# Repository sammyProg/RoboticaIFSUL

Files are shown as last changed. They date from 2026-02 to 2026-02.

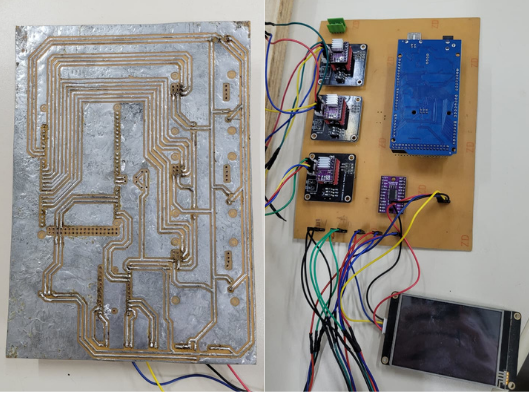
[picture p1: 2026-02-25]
PCB EasyEDA/PCB final.png

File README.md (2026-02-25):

Projeto e Desenvolvimento de um Manipulador Robótico Antropomórfico de 6 GDL (Parcialmente Atuado) para o Ensino da Cinemática Direta

Descrição

Este repositório reúne os arquivos de apoio ao projeto de um manipulador robótico antropomórfico de seis graus de liberdade (6 GDL), parcialmente atuado e impresso em 3D, desenvolvido com finalidade didática para o ensino de cinemática direta.
O projeto foi concebido com foco em:
- visualização prática de conceitos de cinemática direta;
- integração entre modelagem mecânica, eletrônica embarcada e interface homem-máquina;
- validação experimental por comparação entre resultados obtidos via firmware embarcado, MATLAB e visão computacional com marcadores ArUco. 
Observação: embora o manipulador possua 6 GDL, o protótipo é parcialmente atuado, com 3 juntas motorizadas e instrumentadas para os experimentos didáticos, enquanto as demais juntas permanecem fixas no escopo proposto. 

Conteúdo deste repositório

Este repositório foi organizado para concentrar os materiais técnicos utilizados no projeto, incluindo:
- Código-fonte do sistema embarcado (Firmware)
- Controle de motores, leitura de sensores, comunicação com interface e cálculo de cinemática direta embarcada.
- Código-fonte de validação com ArUco
- Rotinas de visão computacional para medição/estimativa de pose e comparação com os resultados do sistema.

Desenhos de referência em SolidWorks
- Desenhos de peças (elos, base, engrenagens etc.)
- Desenho de montagem de conjuntos
- Referências dimensionais para fabricação e montagem do protótipo

Documentação complementar (opcional)
- Esquemático EasyEDA
- Interface IHM Nextion
- Desenho de apoio 2D
  
Materiais auxiliares, imagens, PDFs e instruções para reprodução parcial do sistema.

Conteúdo deste repositório

Este repositório foi organizado para concentrar os materiais técnicos utilizados no projeto, incluindo:
- Código-fonte do sistema embarcado (Firmware)
- Controle de motores, leitura de sensores, comunicação com interface e cálculo de cinemática direta embarcada.
- Código-fonte de validação com ArUco
- Rotinas de visão computacional para medição/estimativa de pose e comparação com os resultados do sistema.
- Desenhos de referência em SolidWorks
- Desenhos de peças (elos, base, engrenagens etc.)
- Desenho de montagem de conjuntos
- Referências dimensionais para fabricação e montagem do protótipo
- Documentação complementar (opcional)
- Materiais auxiliares, imagens, PDFs e instruções para reprodução parcial do sistema.

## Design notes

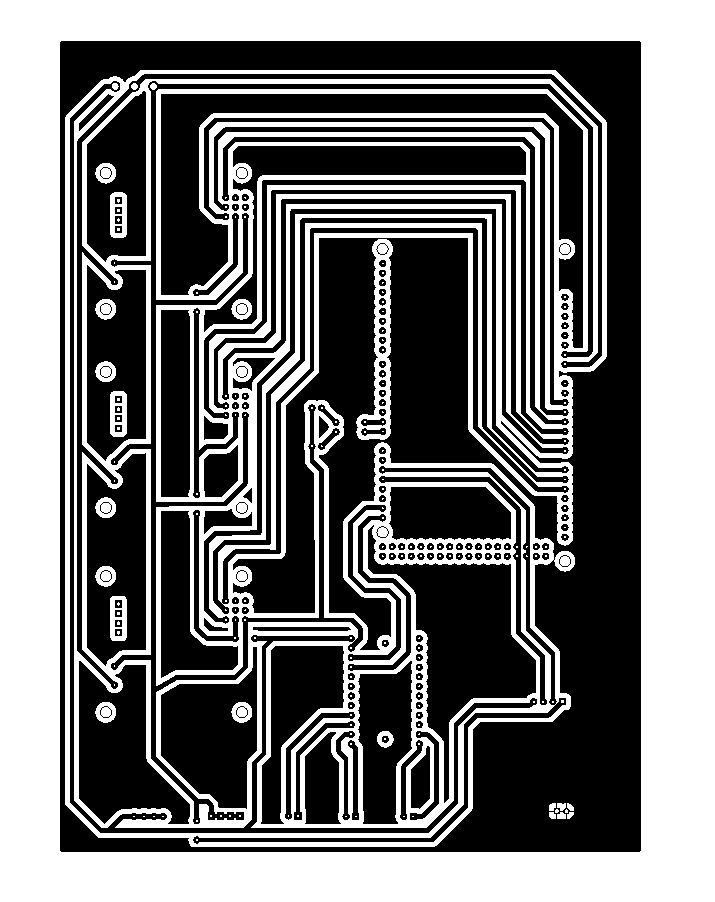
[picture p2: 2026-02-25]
PCB EasyEDA/PCB_PCB_PCB-Braço_2_2026-02-13.png

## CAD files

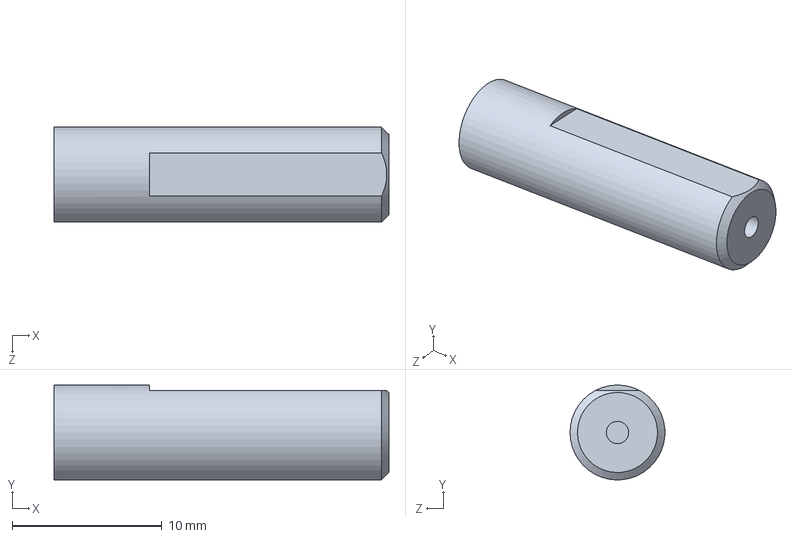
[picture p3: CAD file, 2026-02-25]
SolidWorks/Peças/Conjunto Motor/Eixo motor Nema23.SLDPRT
22.4 x 6.35 x 6.35 mm

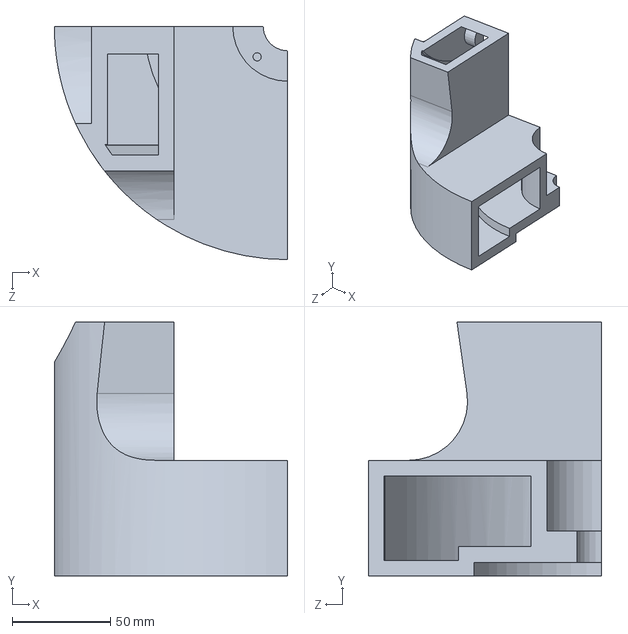
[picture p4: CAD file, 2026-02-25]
SolidWorks/Peças/Elo 1/Elo 1 quadrante 3 baixo.SLDPRT
119.0 x 129.5 x 119.0 mm

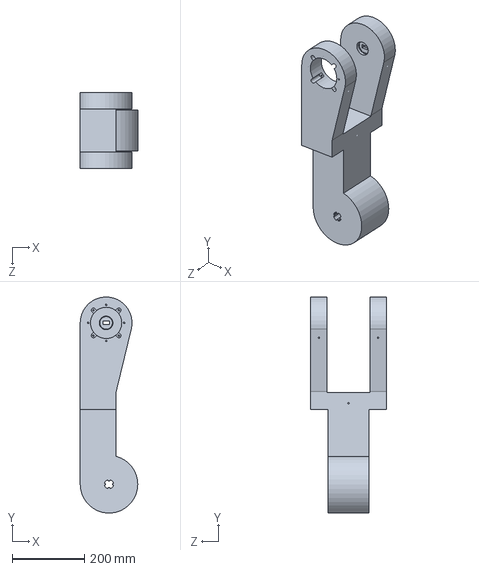
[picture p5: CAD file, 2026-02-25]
SolidWorks/Peças/Elo 2/Elo 2 braço ROB.SLDPRT
160.0 x 599.6 x 210.0 mm

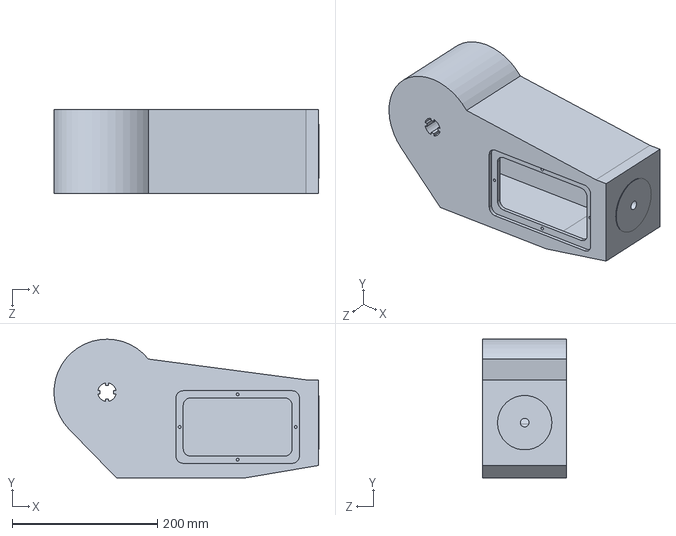
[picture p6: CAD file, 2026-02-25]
SolidWorks/Peças/Elo 3/Elo 3 braço rob.SLDPRT
365.0 x 191.0 x 115.5 mm

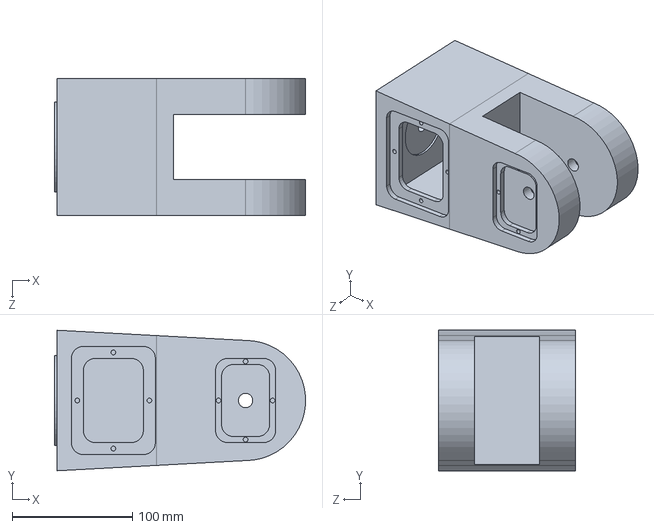
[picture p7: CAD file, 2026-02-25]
SolidWorks/Peças/Elo 4/Elo 4 braço ROB.SLDPRT
208.9 x 117.0 x 114.0 mm

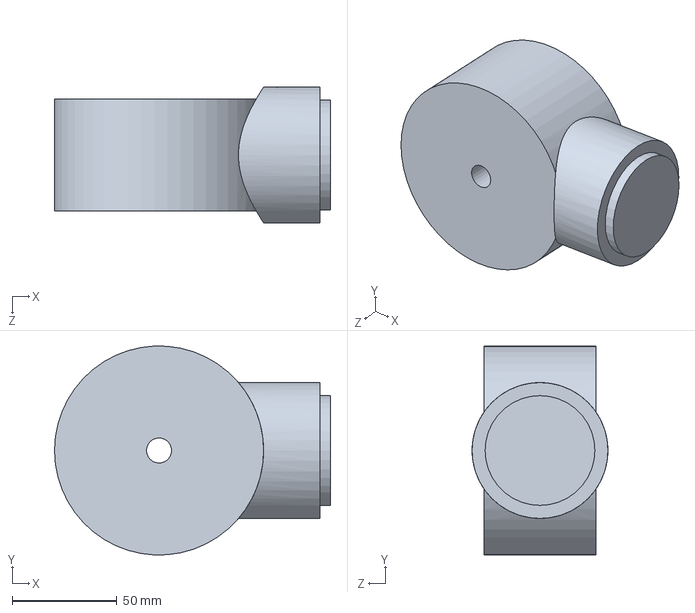
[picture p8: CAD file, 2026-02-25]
SolidWorks/Peças/Elo 5/Elo 5 braço ROB.SLDPRT
132.0 x 99.9 x 65.0 mm

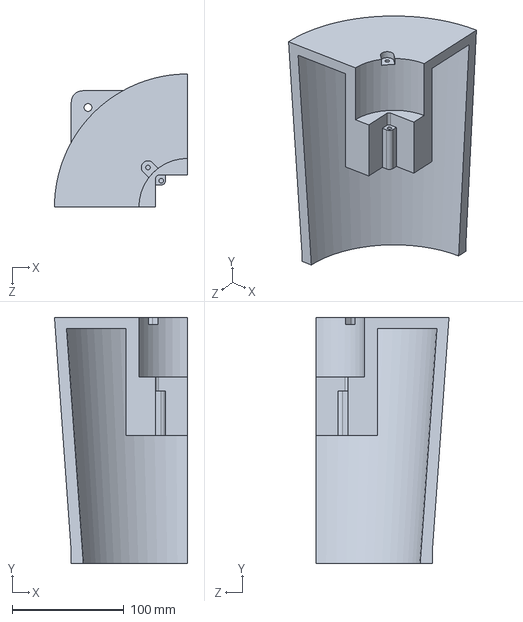
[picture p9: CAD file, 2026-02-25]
SolidWorks/Peças/Elo Base/Base braço ROB quadrante 4.SLDPRT
119.0 x 220.0 x 119.0 mm

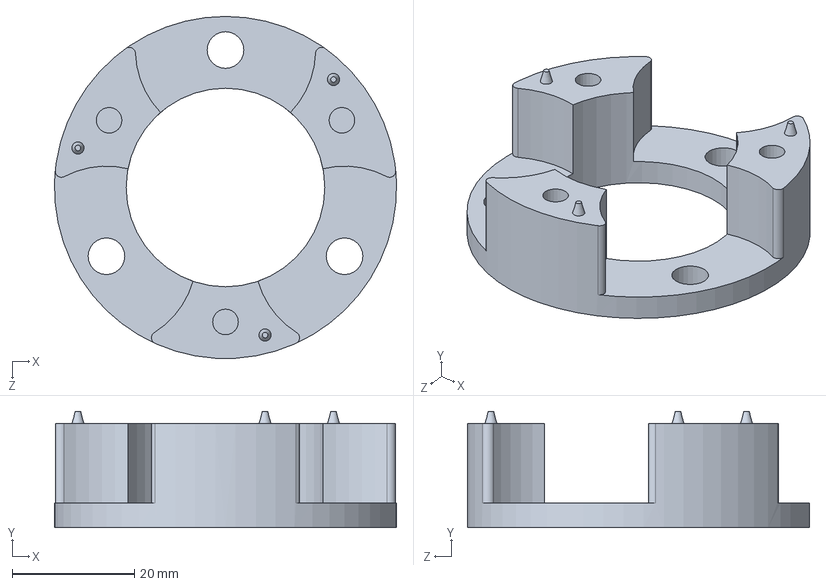
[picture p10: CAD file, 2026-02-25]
SolidWorks/Peças/Engrenagens dentes retos/Peça 5.SLDPRT
56.0 x 19.0 x 56.0 mm

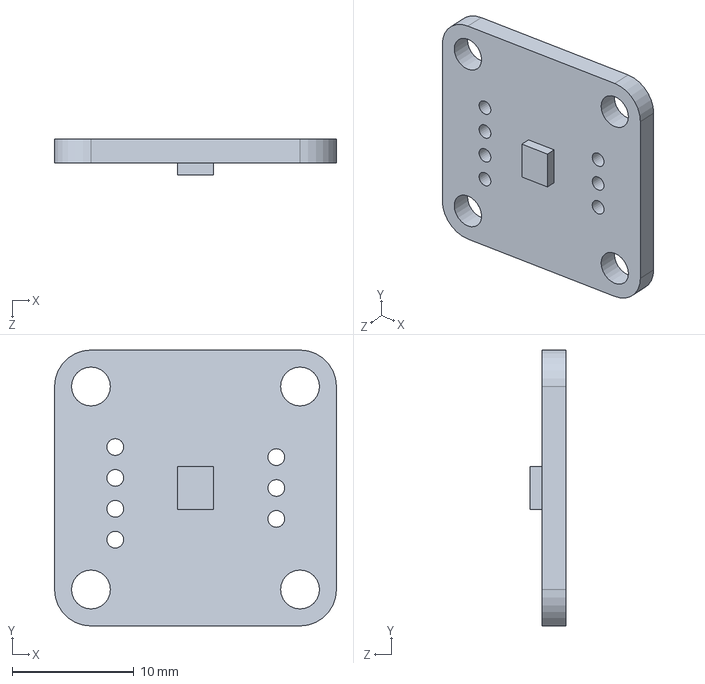
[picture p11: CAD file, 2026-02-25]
SolidWorks/Peças/Conjunto Motor/AS5600.SLDPRT
23.2 x 22.7 x 3.00 mm

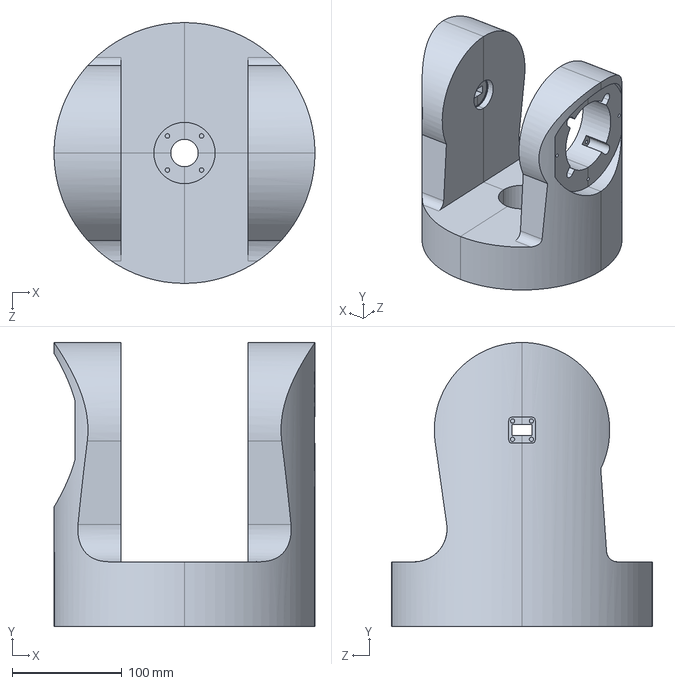
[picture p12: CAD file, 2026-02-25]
SolidWorks/Peças/Elo 1/Elo 1 braço ROB.SLDPRT
238.0 x 259.1 x 238.0 mm

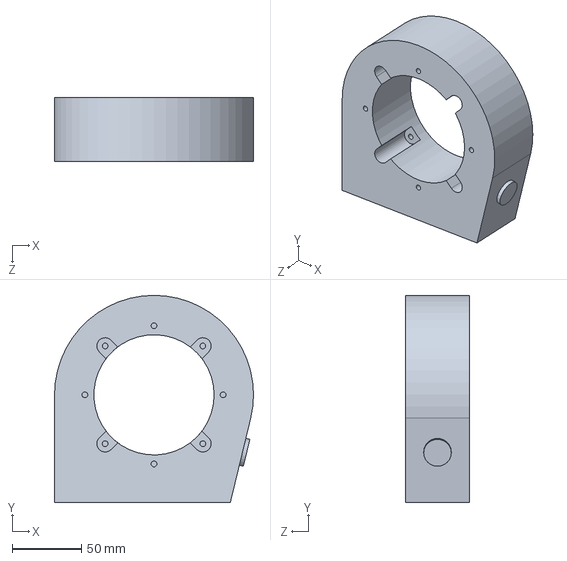
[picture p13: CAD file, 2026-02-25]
SolidWorks/Peças/Elo 2/Elo 2 braço ROB pt 5.SLDPRT
144.0 x 150.0 x 46.0 mm

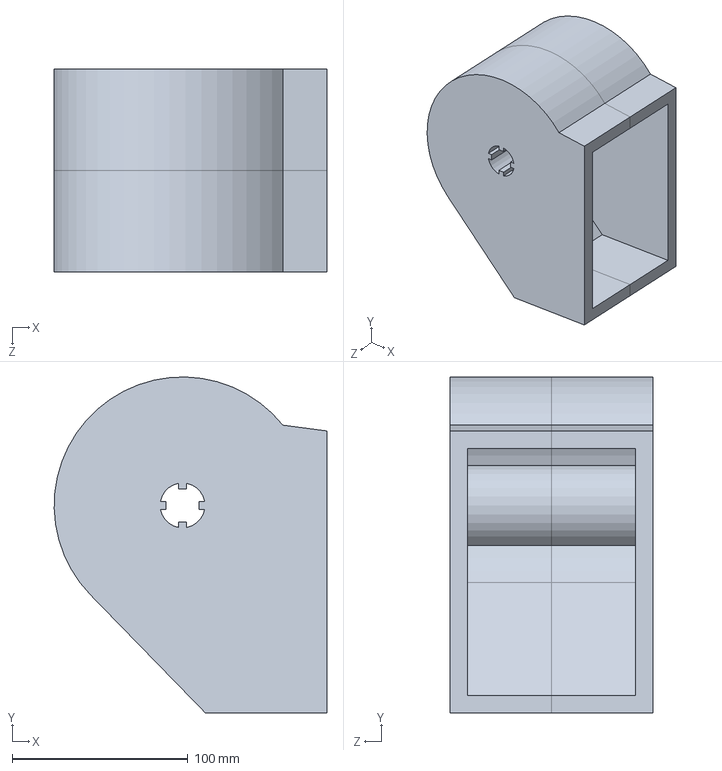
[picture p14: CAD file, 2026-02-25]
SolidWorks/Peças/Elo 3/Elo 3 braço rob pt3.SLDPRT
155.0 x 191.0 x 115.5 mm

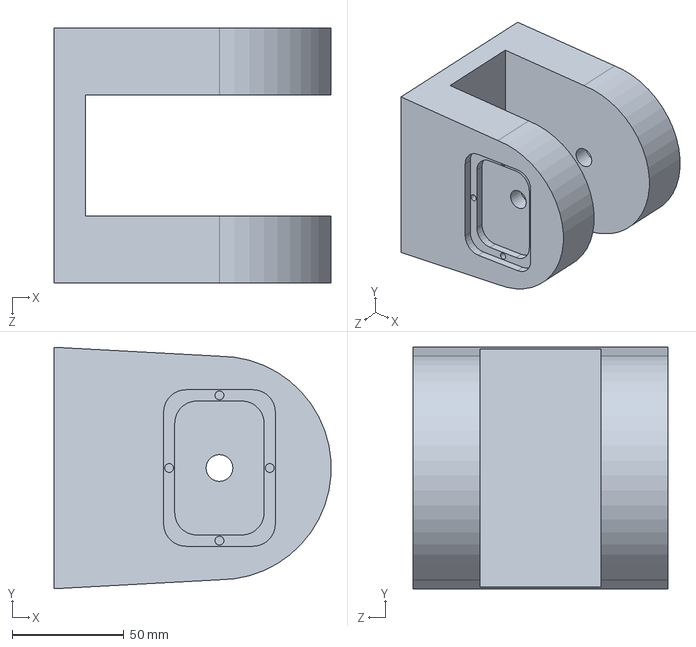
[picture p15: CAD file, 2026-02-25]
SolidWorks/Peças/Elo 4/Elo 4 braço ROB pt2.SLDPRT
123.9 x 108.0 x 114.0 mm

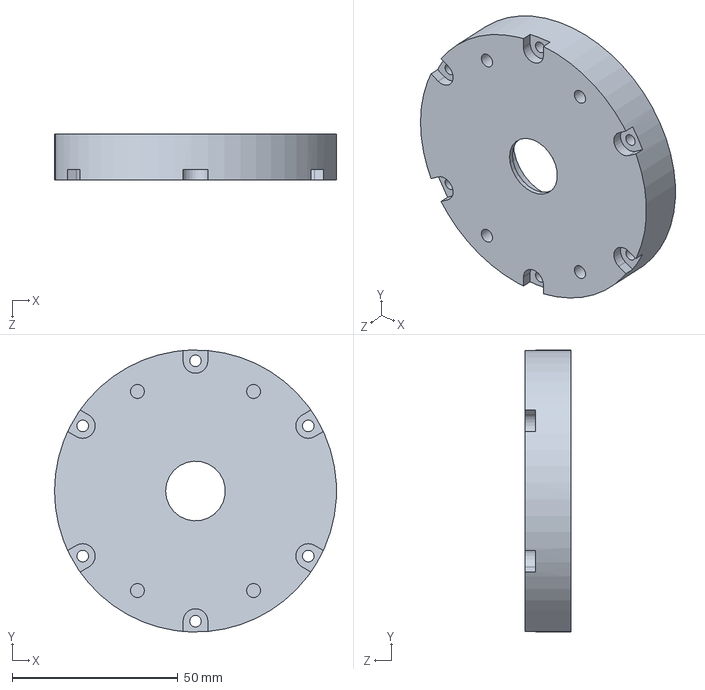
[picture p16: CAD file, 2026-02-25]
SolidWorks/Peças/Engrenagens dentes retos/Peça 8.SLDPRT
85.0 x 85.0 x 14.0 mm

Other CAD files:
SolidWorks/Montagens/Conjunto Motor/MontConjuntoMotor.SLDASM
SolidWorks/Montagens/Engrenagens Planetárias/Montagem Redução dentes retos elo 1.SLDASM
SolidWorks/Montagens/Engrenagens Planetárias/Montagem Redução dentes retos.SLDASM
SolidWorks/Peças/Elo Base/Base braço ROB quadrante 2.SLDPRT
SolidWorks/Peças/Conjunto Motor/Pino central 3mm v2.SLDPRT
SolidWorks/Peças/Conjunto Motor/Pino central.SLDPRT
SolidWorks/Peças/Conjunto Motor/Suporte.SLDPRT
SolidWorks/Peças/Elo 1/Elo 1 quadrante 1 baixo.SLDPRT
SolidWorks/Peças/Elo 1/Elo 1 quadrante 1 cima.SLDPRT
SolidWorks/Peças/Elo 1/Elo 1 quadrante 1.SLDPRT
SolidWorks/Peças/Elo 1/Elo 1 quadrante 2 baixo.SLDPRT
SolidWorks/Peças/Elo 1/Elo 1 quadrante 2 cima.SLDPRT
SolidWorks/Peças/Elo 1/Elo 1 quadrante 2.SLDPRT
SolidWorks/Peças/Elo 1/Elo 1 quadrante 3 cima.SLDPRT
SolidWorks/Peças/Elo 1/Elo 1 quadrante 3.SLDPRT
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

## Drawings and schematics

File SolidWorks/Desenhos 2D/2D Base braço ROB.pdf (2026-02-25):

B

A

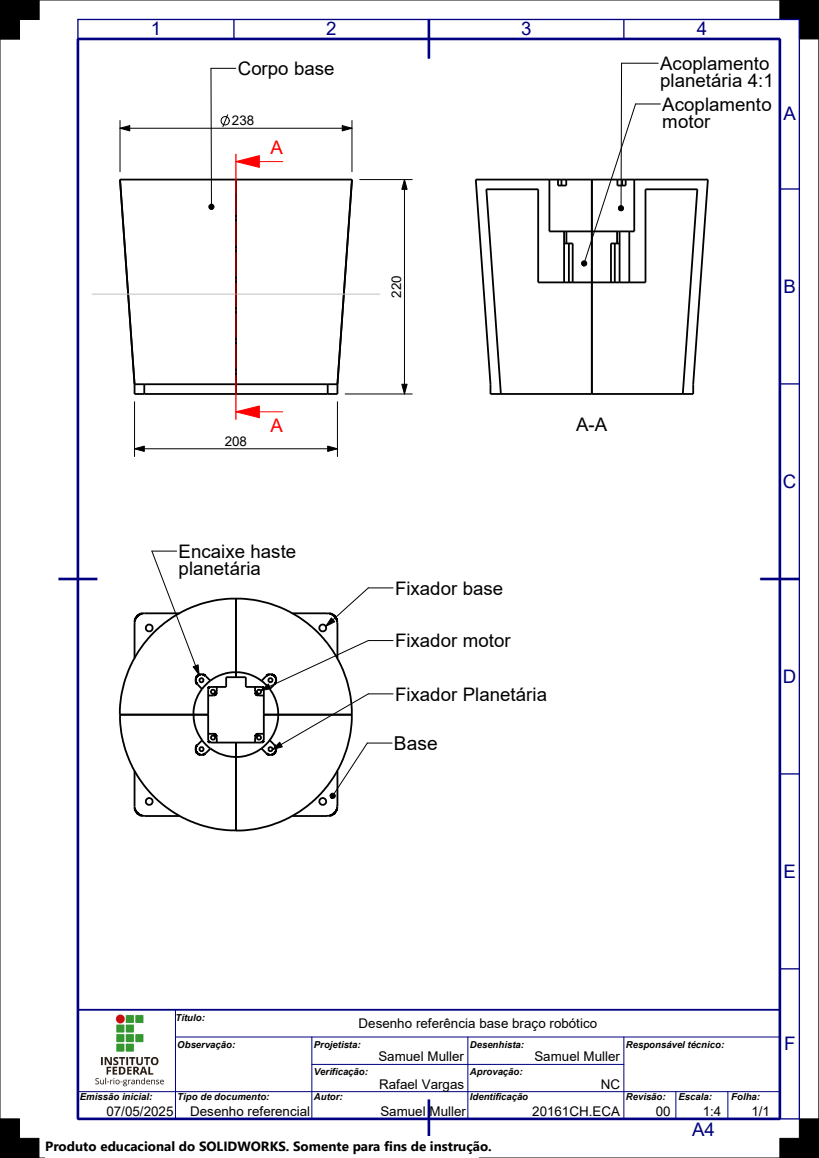
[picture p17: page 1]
Fixador motor; Base; Fixador base; Fixador Planetária; Encaixe haste planetária; Corpo base; Acoplamento planetária 4:1 Acoplamento motor

Título: Desenho referência base braço robótico

Observação: | Projetista: Samuel Muller | Desenhista: Samuel Muller | Responsável técnico:

Verificação: Rafael Vargas | Aprovação: NC

Emissão inicial: 07/05/2025 | Tipo de documento: Desenho referencial | Autor: Samuel Muller | | Identificação | Revisão: 00 20161CH.ECA | Escala: | Folha: 1/1 1:4

Produto educacional do SOLIDWORKS. Somente para fins de instrução.

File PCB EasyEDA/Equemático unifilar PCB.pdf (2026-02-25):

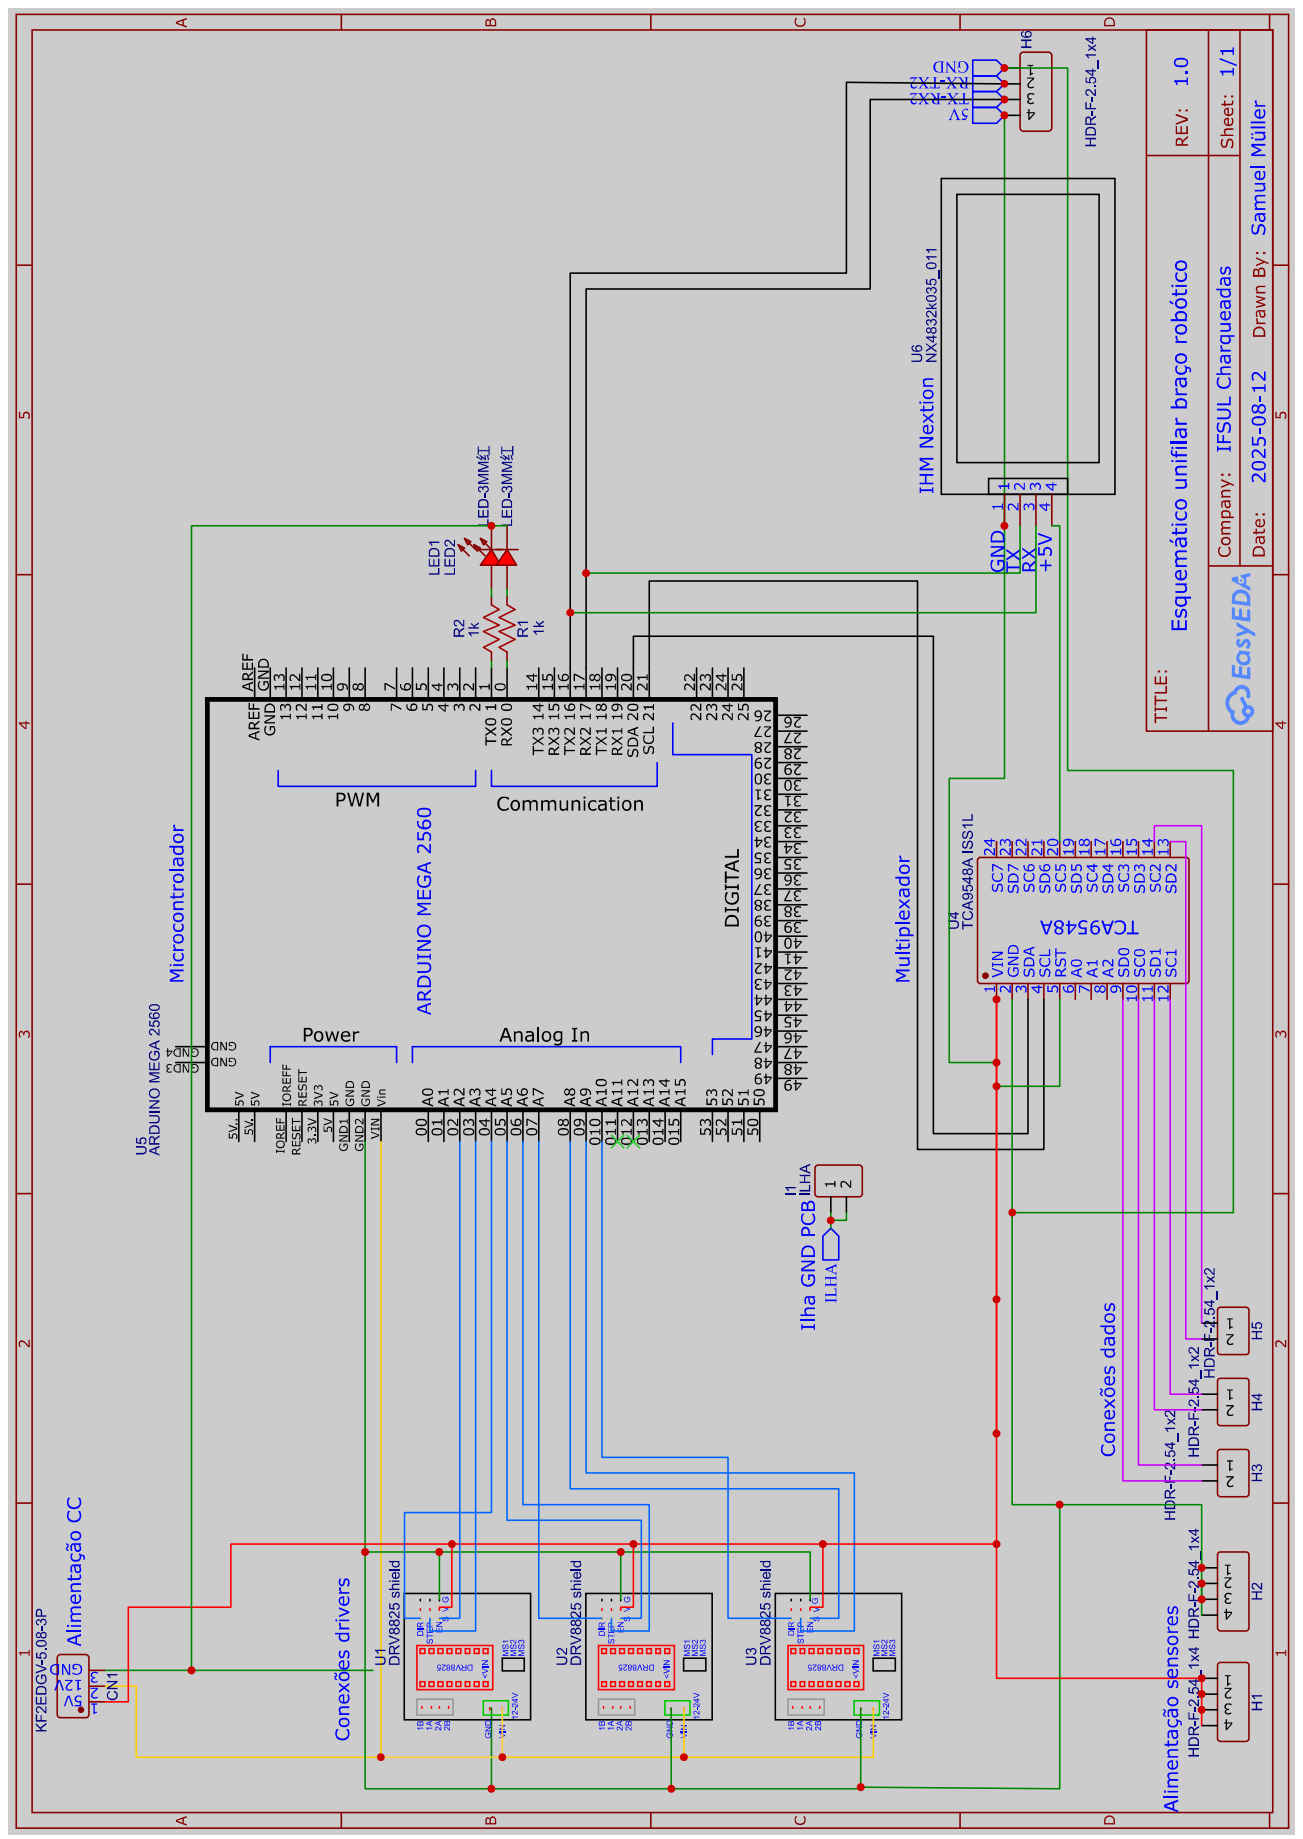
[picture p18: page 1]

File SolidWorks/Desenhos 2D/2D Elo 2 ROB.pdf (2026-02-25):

A

1 | 2 | 3

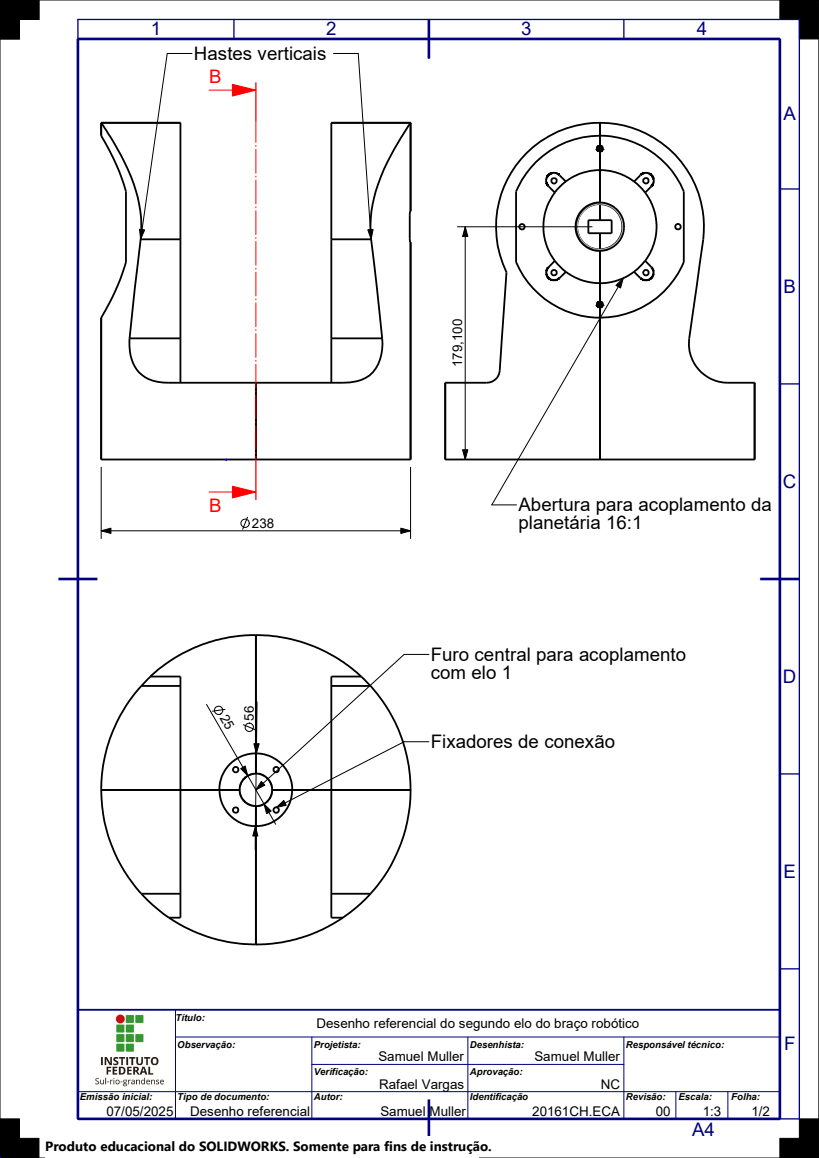
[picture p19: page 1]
Hastes verticais

Desenho referencial do segundo elo do braço robótico ¹⁷⁹,100

Abertura para acoplamento da
planetária 16:1

Furo central para acoplamento
com elo 1

Fixadores de conexão

Título:

Observação: | Projetista: Samuel Muller | Desenhista: Samuel Muller | Responsável técnico:

Verificação: Rafael Vargas | Aprovação: NC

Emissão inicial: 07/05/2025 | Tipo de documento: Desenho referencial | Autor: Samuel Muller | | Identificação | Revisão: 00 20161CH.ECA | Escala: | Folha: 1/2 1:3

Produto educacional do SOLIDWORKS. Somente para fins de instrução.

# Compartimento rolamento

# Abertura para leitura do sensor

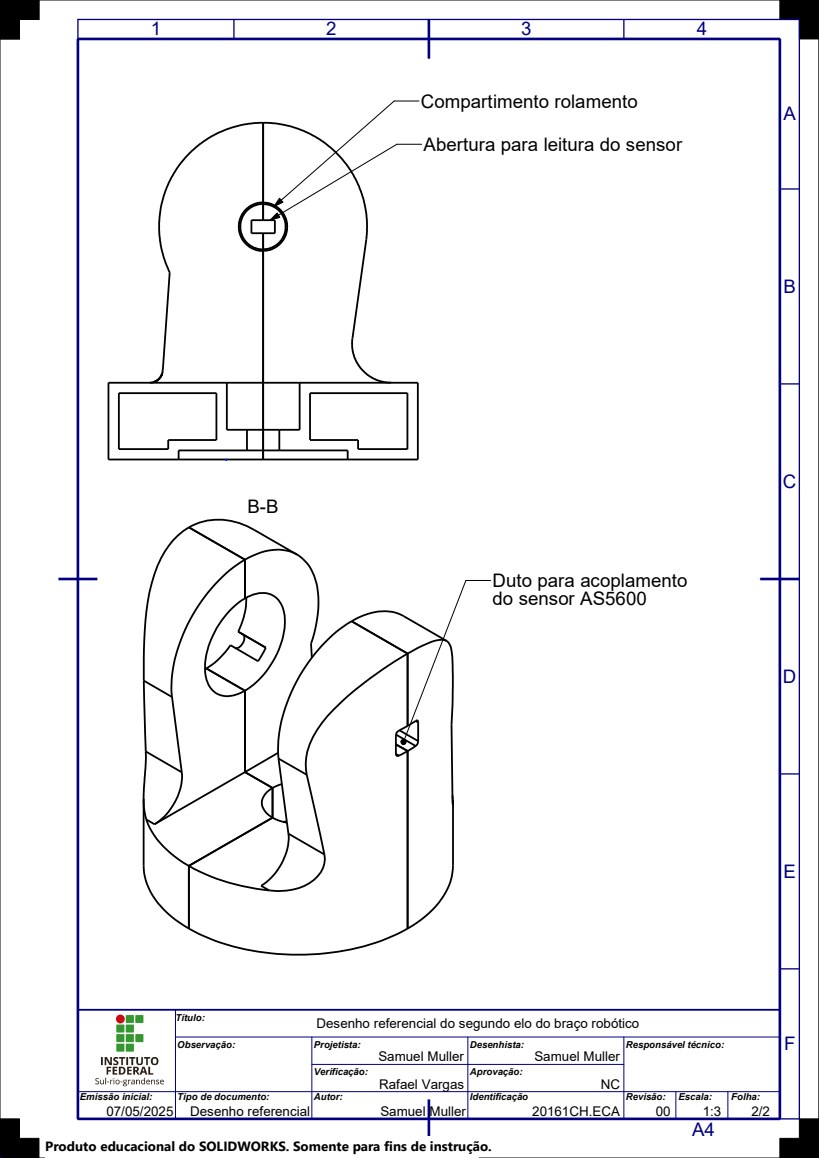
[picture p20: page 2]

Duto para acoplamento
do sensor AS5600

Título: Desenho referencial do segundo elo do braço robótico

Observação: | Projetista: Samuel Muller | Desenhista: Samuel Muller | Responsável técnico:

Verificação: Rafael Vargas | Aprovação: NC

Emissão inicial: 07/05/2025 | Tipo de documento: Desenho referencial | Autor: Samuel Muller | | Identificação | Revisão: 00 20161CH.ECA | Escala: | Folha: 2/2 1:3

Produto educacional do SOLIDWORKS. Somente para fins de instrução.

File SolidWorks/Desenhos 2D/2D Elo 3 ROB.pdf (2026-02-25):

3

B

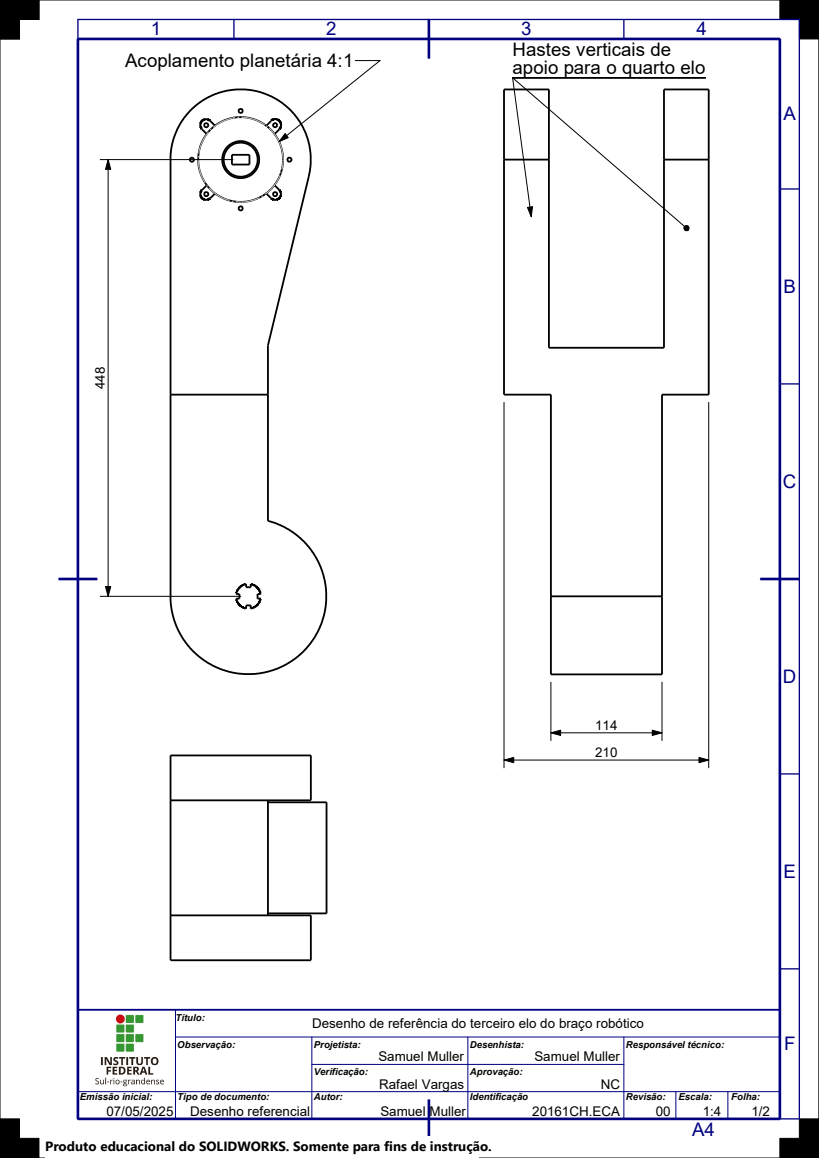
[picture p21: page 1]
Acoplamento planetária 4:1; apoio para o quarto elo

Hastes verticais de

Desenho de referência do terceiro elo do braço robótico ⁴⁴⁸

Título:

Observação: | Projetista: Samuel Muller | Desenhista: Samuel Muller | Responsável técnico:

Verificação: Rafael Vargas | Aprovação: NC

Emissão inicial: 07/05/2025 | Tipo de documento: Desenho referencial | Autor: Samuel Muller | | Identificação | Revisão: 00 20161CH.ECA | Escala: | Folha: 1/2 1:4

Produto educacional do SOLIDWORKS. Somente para fins de instrução.

B

A

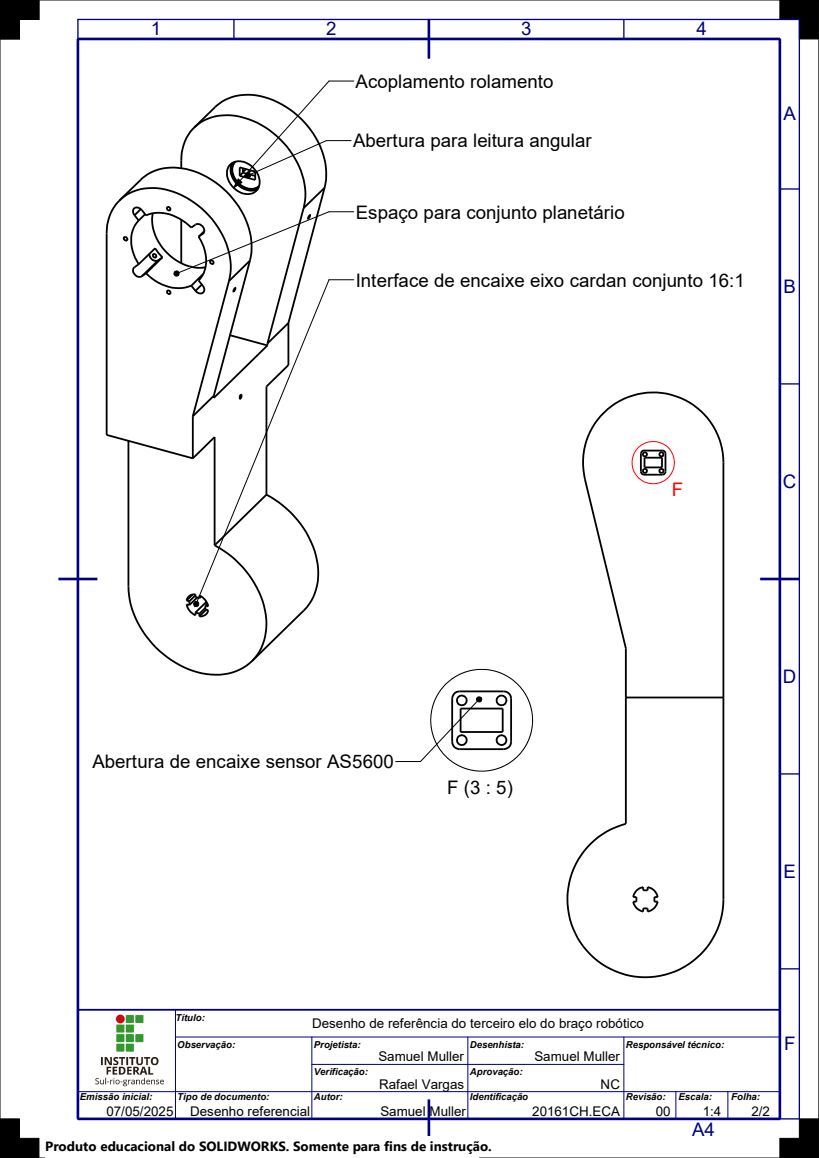
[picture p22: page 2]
Acoplamento rolamento

Abertura para leitura angular

Espaço para conjunto planetário

Interface de encaixe eixo cardan conjunto 16:1

Abertura de encaixe sensor AS5600

Título: Desenho de referência do terceiro elo do braço robótico

Observação: | Projetista: Samuel Muller | Desenhista: Samuel Muller | Responsável técnico:

Verificação: Rafael Vargas | Aprovação: NC

Emissão inicial: 07/05/2025 | Tipo de documento: Desenho referencial | Autor: Samuel Muller | | Identificação | Revisão: 00 20161CH.ECA | Escala: | Folha: 2/2 1:4

Produto educacional do SOLIDWORKS. Somente para fins de instrução.

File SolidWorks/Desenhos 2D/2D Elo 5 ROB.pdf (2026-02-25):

2 3

B

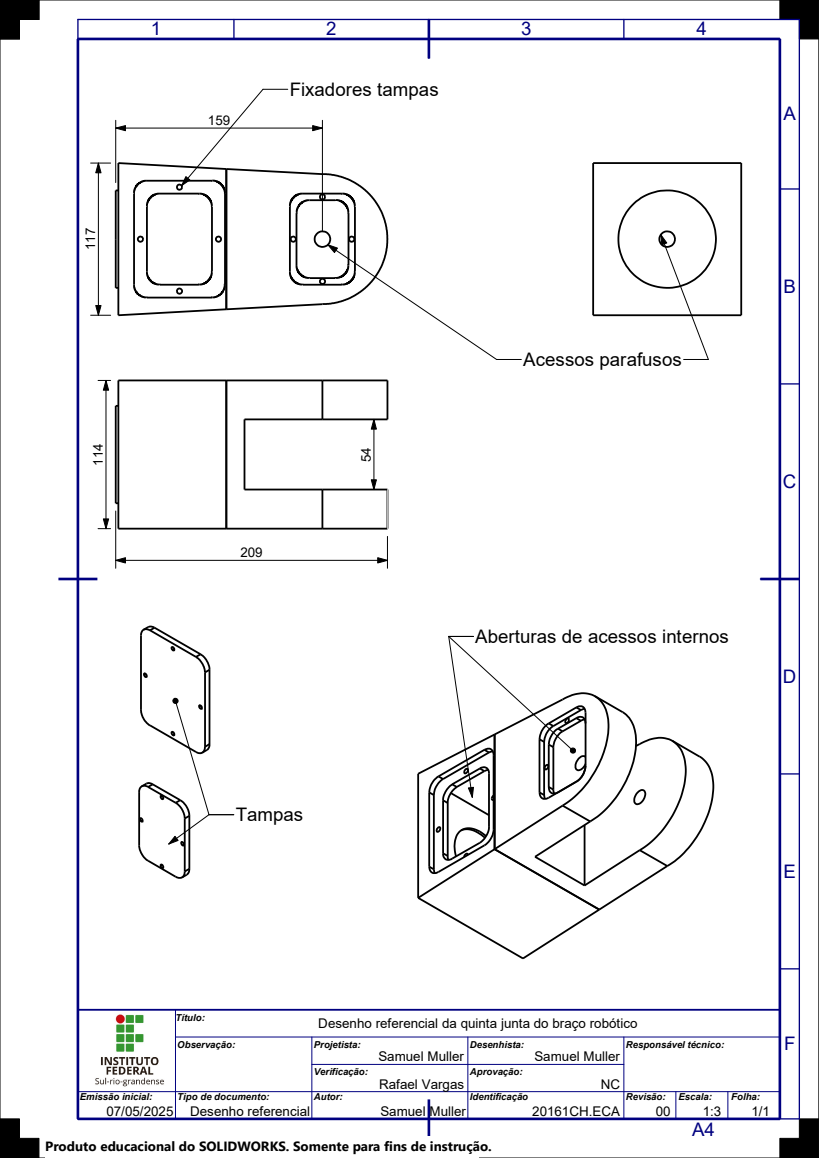
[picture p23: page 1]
Acessos parafusos; Fixadores tampas; Tampas

Aberturas de acessos internos

Título: Desenho referencial da quinta junta do braço robótico

Observação: | Projetista: Samuel Muller | Desenhista: Samuel Muller | Responsável técnico:

Verificação: Rafael Vargas | Aprovação: NC

Emissão inicial: 07/05/2025 | Tipo de documento: Desenho referencial | Autor: Samuel Muller | | Identificação | Revisão: 00 20161CH.ECA | Escala: | Folha: 1/1 1:3

Produto educacional do SOLIDWORKS. Somente para fins de instrução.

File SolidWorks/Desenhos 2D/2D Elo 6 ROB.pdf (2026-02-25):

3

B

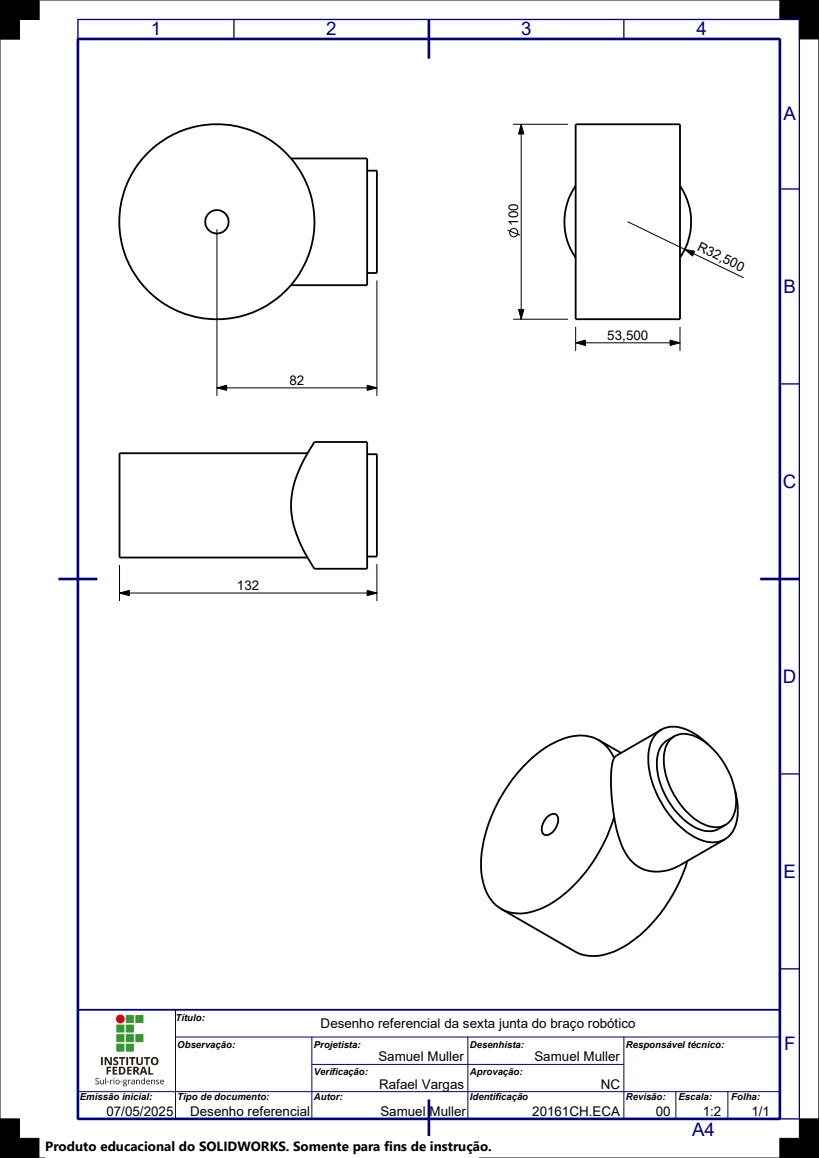
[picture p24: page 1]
53,500 ¹⁰⁰

Título: Desenho referencial da sexta junta do braço robótico

Observação: | Projetista: Samuel Muller | Desenhista: Samuel Muller | Responsável técnico:

Verificação: Rafael Vargas | Aprovação: NC

Emissão inicial: 07/05/2025 | Tipo de documento: Desenho referencial | Autor: Samuel Muller | | Identificação | Revisão: 00 20161CH.ECA | Escala: | Folha: 1/1 1:2

Produto educacional do SOLIDWORKS. Somente para fins de instrução.

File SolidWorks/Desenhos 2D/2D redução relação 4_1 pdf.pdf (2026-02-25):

A A

## Tampa superior

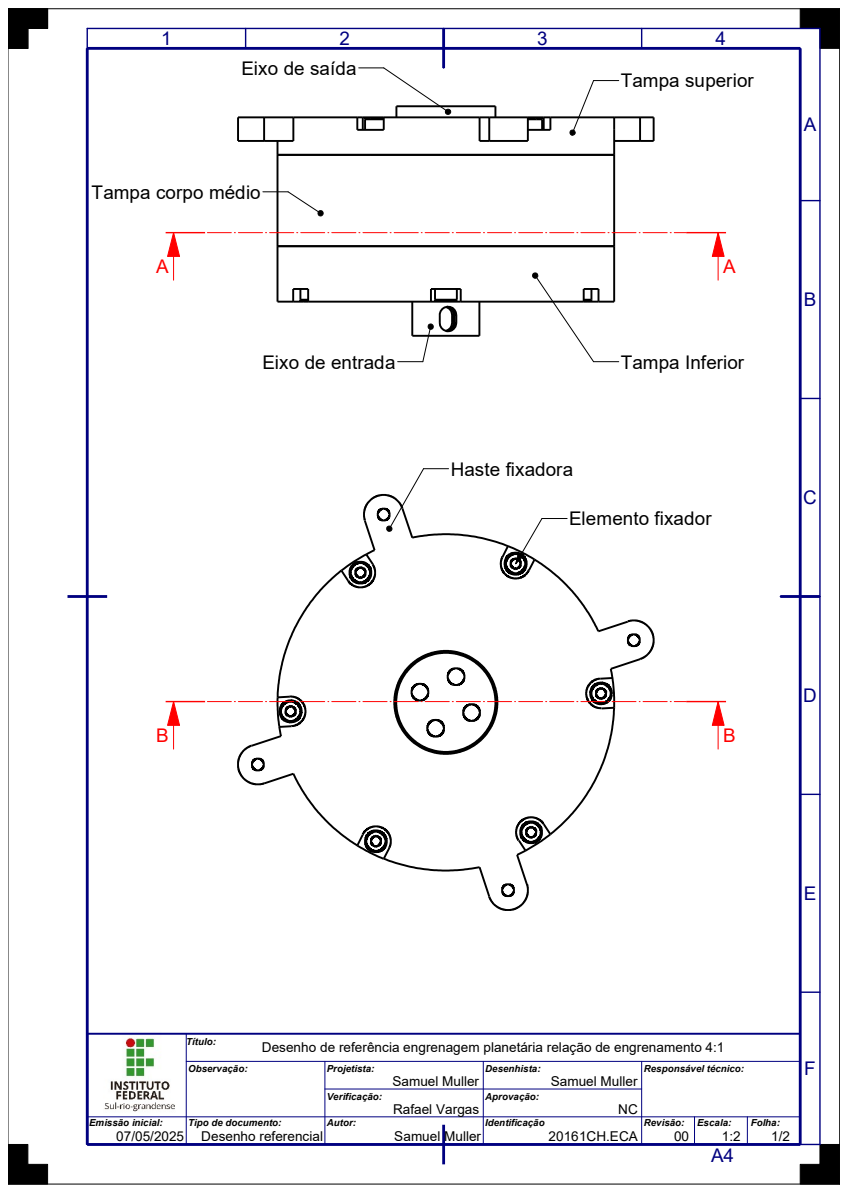
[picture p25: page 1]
Eixo de entrada; Tampa Inferior; Haste fixadora; Elemento fixador

Eixo de saída

Tampa corpo médio

Título: Desenho de referência engrenagem planetária relação de engrenamento 4:1

Observação: | Projetista: Samuel Muller | Desenhista: Samuel Muller | Responsável técnico:

Verificação: Rafael Vargas | Aprovação: NC

Emissão inicial: 07/05/2025 | Tipo de documento: Desenho referencial | Autor: Samuel Muller | | Identificação | Revisão: 00 20161CH.ECA | Escala: | Folha: 1/2 1:2

2 3

A

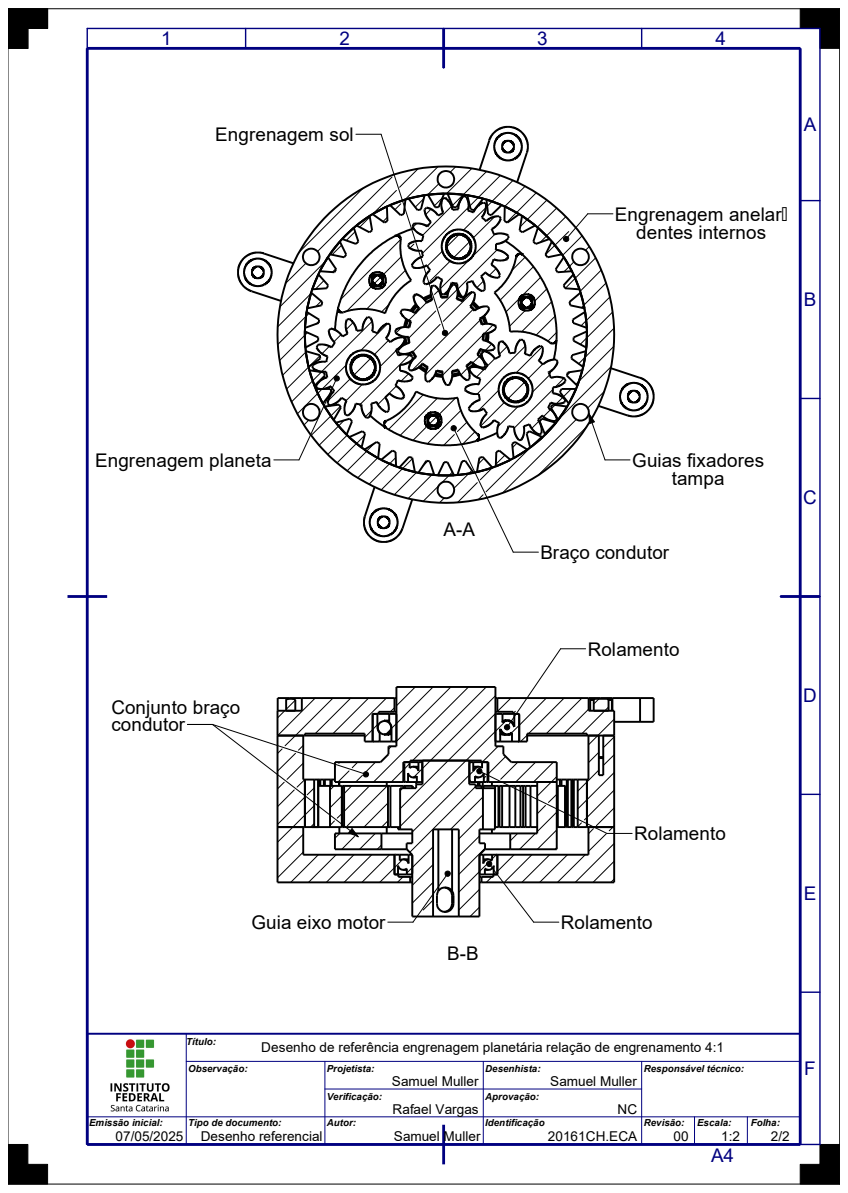
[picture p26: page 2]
Engrenagem anelar dentes internos; Guias fixadores tampa; Braço condutor; Engrenagem sol; Engrenagem planeta; Rolamento; Conjunto braço condutor

Guia eixo motor

Título: Desenho de referência engrenagem planetária relação de engrenamento 4:1

Observação: | Projetista: Samuel Muller | Desenhista: Samuel Muller | Responsável técnico:

Verificação: Rafael Vargas | Aprovação: NC

Emissão inicial: 07/05/2025 | Tipo de documento: Desenho referencial | Autor: Samuel Muller | | Identificação | Revisão: 00 20161CH.ECA | Escala: | Folha: 2/2 1:2

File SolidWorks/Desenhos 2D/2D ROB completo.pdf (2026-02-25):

2 3

B

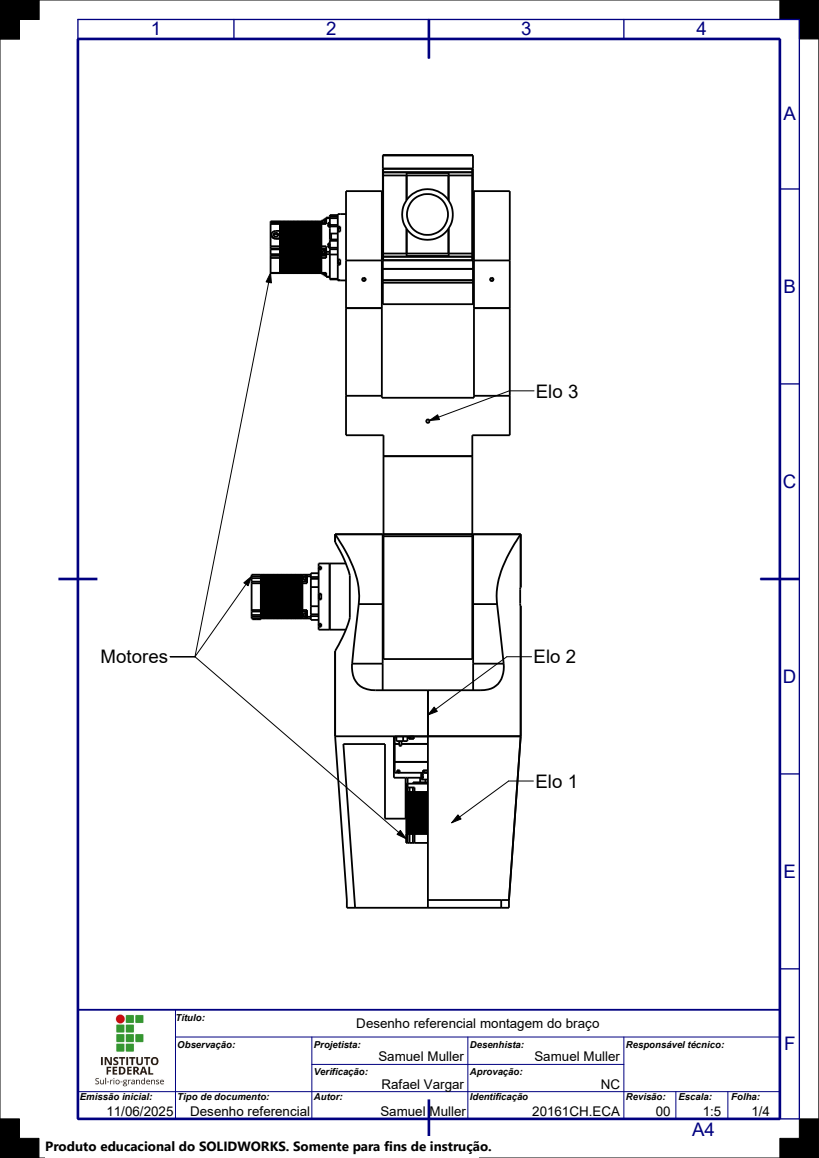
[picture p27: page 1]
Elo 2; Elo 3; Elo 1; Motores

Título: Desenho referencial montagem do braço

Observação: | Projetista: Samuel Muller | Desenhista: Samuel Muller | Responsável técnico:

Verificação: Rafael Vargar | Aprovação: NC

Emissão inicial: 11/06/2025 | Tipo de documento: Desenho referencial | Autor: Samuel Muller | | Identificação | Revisão: 00 20161CH.ECA | Escala: | Folha: 1/4 1:5

Produto educacional do SOLIDWORKS. Somente para fins de instrução.

## Desenho referencial montagem do braço ⁴²

B

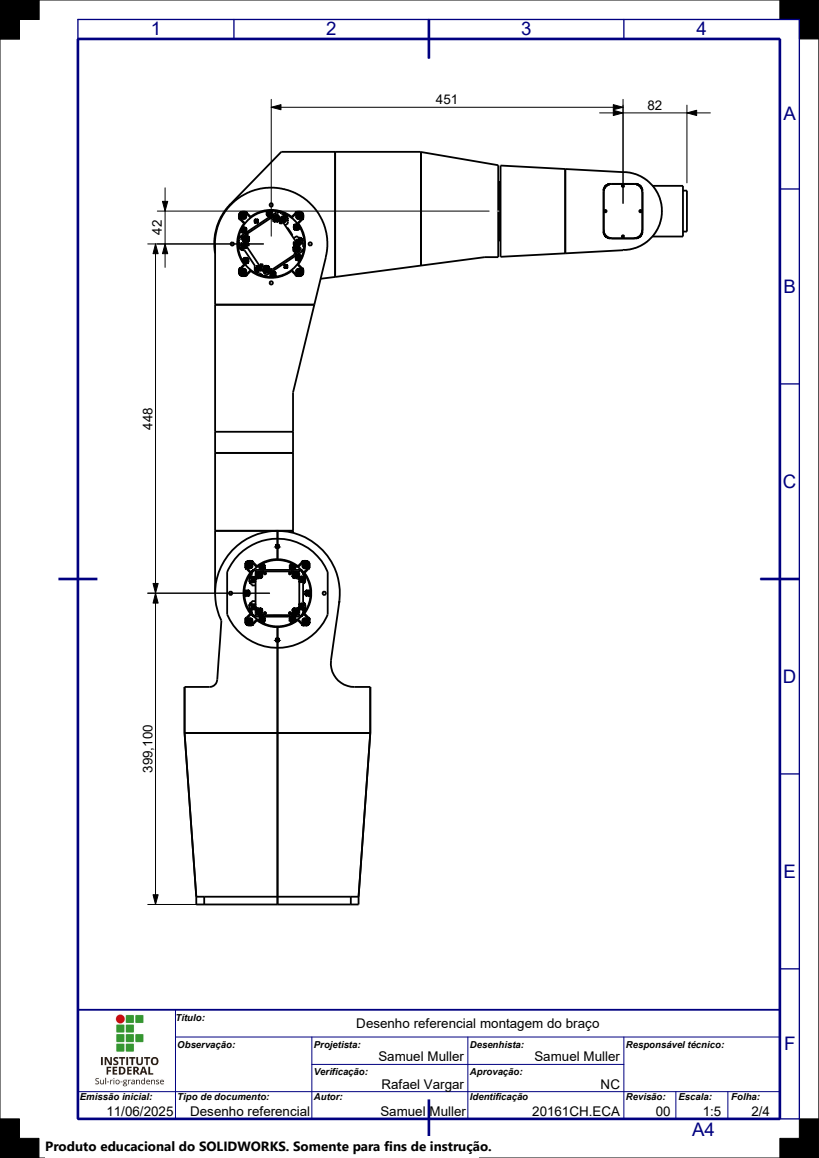
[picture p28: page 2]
Desenho referencial; 00 20161CH.ECA

Título:

Observação: | Projetista: Samuel Muller | Desenhista: Samuel Muller | Responsável técnico:

B

A

Desenho referencial; 00 20161CH.ECA; Elo 4; Elo 5; Elo 6

Título: Desenho referencial montagem do braço

Observação: | Projetista: Samuel Muller | Desenhista: Samuel Muller | Responsável técnico:

B

A

Desenho referencial; 00 20161CH.ECA

Título: Desenho referencial montagem do braço

Observação: | Projetista: Samuel Muller | Desenhista: Samuel Muller | Responsável técnico:

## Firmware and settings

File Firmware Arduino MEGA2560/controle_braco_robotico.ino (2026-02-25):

// ============================================================================
// Objetivo geral do codigo
// ----------------------------------------------------------------------------
// Este programa implementa o controle de 3 juntas de um braco robotico usando:
// - IHM Nextion (3 sliders) para definir posicao alvo das juntas (em graus)
// - 3 motores de passo via drivers DRV8825 (STEP/DIR/EN) usando AccelStepper
// - 3 sensores magneticos AS5600 (via I2C) para medir os angulos reais
// - Multiplexador I2C PCA9548A para compartilhar o barramento I2C entre sensores
// - Calculo de cinematica direta via matrizes 4x4 (DH) para obter x,y,z
// - Envio para o Nextion dos angulos (t0..t5) e coordenadas (t6..t8)
//
// Fluxo logico principal:
// 1) setup: inicializa Serial, Nextion, I2C, sensores, drivers e motores
// 2) setup: le sliders uma vez e sincroniza posicao atual dos motores (evita tranco)
// 3) loop: le sliders -> converte para passos -> move motores para alvos
// 4) loop: le sensores -> corrige offsets/normaliza -> mostra no display
// 5) loop: converte graus->rad -> monta A1..A6 -> multiplica -> extrai x,y,z
// 6) loop: envia x,y,z ao display
// ============================================================================

#include <AccelStepper.h>
#include <Wire.h>
#include <AS5600.h>
#include <Nextion.h>
#include <math.h>

// Endereco do multiplexador I2C PCA9548A
#define PCA9548A_ADDRESS 0x70

// Constante PI (evita depender de definicoes externas)
#define PI 3.1415926535897932384626433832795

// Flags usadas para "ignorar" o primeiro comando de movimento em algumas juntas
// Ideia: na primeira iteracao, apenas marca como inicializado e nao move
bool init1_done = false;
bool init2_done = false;
bool init3_done = false;

// Variaveis para leitura inicial dos sliders (evitar movimento no boot)
uint32_t val00 = 0, val11 = 180, val22 = 180;

// Targets iniciais em passos (posicao alvo equivalente aos sliders no boot)
long target11 = 0, target22 = 0, target33 = 0;

// ---------------------------------------------------------------------------
// 1) Declaracao dos sensores AS5600
// ---------------------------------------------------------------------------
AS5600 as5600_1;
AS5600 as5600_2;
AS5600 as5600_3;

// ---------------------------------------------------------------------------
// 2) Declaracao do Nextion: sliders (h0,h1,h2) e textos (t0..t8)
// ---------------------------------------------------------------------------
// Sliders: representam comando de posicao (graus) para cada junta motorizada
NexSlider h0 = NexSlider(0, 1, "h0");
NexSlider h1 = NexSlider(0, 3, "h1");
NexSlider h2 = NexSlider(0, 6, "h2");

// Lista de elementos touch que podem gerar eventos (na pratica aqui so le valor)
NexTouch *nrx_listen_list[] = {
  &h0, &h1, &h2,
  NULL
};

// Textos no Nextion:
// t0..t5: angulos das 6 articulacoes (3 reais + 3 fixas)
// t6..t8: coordenadas x,y,z do efetuador final
NexText t0 = NexText(0, 2, "t0");
NexText t1 = NexText(0, 4, "t1");
NexText t2 = NexText(0, 5, "t2");
NexText t3 = NexText(0, 7, "t3");
NexText t4 = NexText(0, 8, "t4");
NexText t5 = NexText(0, 9, "t5");
NexText t6 = NexText(0, 11, "t6");
NexText t7 = NexText(0, 10, "t7");
NexText t8 = NexText(0, 12, "t8");

// ---------------------------------------------------------------------------
// 3) Declaracao dos motores (DRV8825 + AccelStepper)
// ---------------------------------------------------------------------------
// Pinos ENABLE de cada driver (LOW habilita, conforme seu codigo)
#define PIN_EN1 56
#define PIN_STEP1 57
#define PIN_DIR1 58

#define PIN_EN2 59
#define PIN_STEP2 60
#define PIN_DIR2 61

#define PIN_EN3 62
#define PIN_STEP3 63
#define PIN_DIR3 64

// AccelStepper em modo DRIVER: so precisa STEP e DIR
AccelStepper stepper1(AccelStepper::DRIVER, PIN_STEP1, PIN_DIR1);
AccelStepper stepper2(AccelStepper::DRIVER, PIN_STEP2, PIN_DIR2);
AccelStepper stepper3(AccelStepper::DRIVER, PIN_STEP3, PIN_DIR3);

// ---------------------------------------------------------------------------
// 4) Selecao de canal no PCA9548A
// ---------------------------------------------------------------------------
// O PCA9548A permite selecionar qual "ramo" I2C fica ativo.
// Assim, varios AS5600 podem ter o mesmo endereco e ainda assim funcionar.
void selectI2CChannel(uint8_t channel) {
  if (channel > 7) return;                 // PCA9548A tem 8 canais: 0..7
  Wire.beginTransmission(PCA9548A_ADDRESS);
  Wire.write(1 << channel);                // habilita apenas o canal desejado
  Wire.endTransmission();
}

// ---------------------------------------------------------------------------
// 5) Conversao do AS5600 (0..4095) para graus (0..360)
// ---------------------------------------------------------------------------
// O AS5600 fornece 12 bits de angulo: 0 a 4095 (teorico).
// Mapeia linearmente para graus.
float mapAngleTo360(uint16_t rawAngle) {
  return (rawAngle * 360.0) / 4095.0;
}

// ---------------------------------------------------------------------------
// 6) Multiplicacao de matrizes 4x4 (cinematica direta)
// ---------------------------------------------------------------------------
// Multiplica a*b e armazena em result.
// Usa temp para evitar sobrescrever caso result seja o mesmo ponteiro.
void multiplyMatrices(double a[4][4], double b[4][4], double result[4][4]) {
  double temp[4][4];

  for (int i = 0; i < 4; i++) {
    for (int j = 0; j < 4; j++) {
      temp[i][j] = 0;
      for (int k = 0; k < 4; k++) {
        temp[i][j] += a[i][k] * b[k][j];
      }
    }
  }

  for (int i = 0; i < 4; i++) {
    for (int j = 0; j < 4; j++) {
      result[i][j] = temp[i][j];
    }
  }
}

void setup() {

  // Serial para debug/monitoramento (nao esta sendo usado no loop)
  Serial.begin(9600);

  // Inicializa comunicacao com Nextion
  nexInit();

  // -----------------------
  // I2C para os AS5600
  // -----------------------
  Wire.begin();                             // inicia I2C como master
  as5600_1.begin(AS5600_DEFAULT_ADDRESS);    // instancia sensor 1
  as5600_2.begin(AS5600_DEFAULT_ADDRESS);    // instancia sensor 2
  as5600_3.begin(AS5600_DEFAULT_ADDRESS);    // instancia sensor 3
  selectI2CChannel(0);                       // seleciona canal 0 como padrao

  // -----------------------
  // Configuracao DRV8825
  // -----------------------
  pinMode(PIN_EN1, OUTPUT);
  digitalWrite(PIN_EN1, LOW);               // habilita driver 1

  pinMode(PIN_EN2, OUTPUT);
  digitalWrite(PIN_EN2, LOW);               // habilita driver 2

  pinMode(PIN_EN3, OUTPUT);
  digitalWrite(PIN_EN3, LOW);               // habilita driver 3

  // Ajuste de limites de velocidade e aceleracao (unidade: passos/seg e passos/seg^2)
  stepper1.setMaxSpeed(500.0);
  stepper1.setAcceleration(100.0);

  stepper2.setMaxSpeed(1000.0);
  stepper2.setAcceleration(500.0);

  stepper3.setMaxSpeed(500.0);
  stepper3.setAcceleration(100.0);

  // =======================================================
  // Leitura inicial dos sliders para evitar movimento no boot
  // -------------------------------------------------------
  // Problema tipico: ao ligar, o motor esta em uma posicao, mas o software
  // "acha" que esta em 0. Ao ler o slider e setar como posicao atual, voce
  // sincroniza referencia e evita um deslocamento brusco.
  // =======================================================

  h0.getValue(&val00);
  h1.getValue(&val11);
  h2.getValue(&val22);

  // Conversao graus -> passos
  // Observacao: usa sinal negativo. Isso define convencao de sentido do motor.
  // As escalas (25600, 102400, 25600) representam passos por volta (inclui microstepping e reducoes).
  target11 = -map(val00, 0, 360, 0, 25600);
  target22 = -map(val11, 0, 360, 0, 102400);
  target33 = -map(val22, 0, 360, 0, 25600);

  // Sincroniza posicao atual interna do AccelStepper com o valor lido do slider
  // Assim, a primeira referencia nao gera movimento inesperado.
  stepper1.setCurrentPosition(target11);
  stepper2.setCurrentPosition(target22);
  stepper3.setCurrentPosition(target33);
}

void loop() {

  // -------------------------------------------------------------------------
  // 1) Leitura dos sliders (comandos do usuario)
  // -------------------------------------------------------------------------
  uint32_t val0, val1, val2;
  h0.getValue(&val0);
  h1.getValue(&val1);
  h2.getValue(&val2);

  // -------------------------------------------------------------------------
  // 2) Conversao de graus (0..360) para passos (0..N)
  // -------------------------------------------------------------------------
  // N define quantos passos correspondem a uma volta completa da junta.
  // Sinal negativo inverte o sentido do movimento.
  long target1 = -map(val0, 0, 360, 0, 25600);
  long target2 = -map(val1, 0, 360, 0, 102400);
  long target3 = -map(val2, 0, 360, 0, 25600);

  // -------------------------------------------------------------------------
  // 3) Movimento dos motores ate a nova posicao
  // -------------------------------------------------------------------------
  // runToNewPosition() e bloqueante: ele so retorna quando atingir o alvo.
  // Consequencia: enquanto um motor esta indo ao alvo, o resto do loop "para".
  // Isso reduz responsividade de leitura de sensores e atualizacao do display.

  // Junta 1: aqui nao ha logica de ignorar o primeiro movimento, ele sempre executa
  stepper1.runToNewPosition(target1);

  // Junta 2: ignora o primeiro comando (marca init2_done e nao move na 1a vez)
  if (!init2_done) {
    init2_done = true;
  } else {
    stepper2.runToNewPosition(target2);
  }

  // Junta 3: idem
  if (!init3_done) {
    init3_done = true;
  } else {
    stepper3.runToNewPosition(target3);
  }

  // -------------------------------------------------------------------------
  // 4) Leitura dos sensores (AS5600) via multiplexador PCA9548A
  // -------------------------------------------------------------------------
  // Sensor 1: possui tratamento de "voltas" para obter angulo absoluto
  // (detecao de rollover 359->0 e 0->359).

  selectI2CChannel(0);
  uint16_t raw1 = as5600_1.readAngle();

  // Converte para graus (nota: aqui voce usa 4096.0 no denominador)
  float ang_motor = (float)raw1 * 360.0 / 4096.0;

  // Variaveis estaticas persistem entre iteracoes do loop
  static float last_ang = ang_motor;
  static long voltas = 0;

  // Diferenca entre amostras
  float diff = ang_motor - last_ang;

  // Detecao de rollover:
  // - Se diff > 180: provavelmente saiu de perto de 0 e foi para perto de 360 (na amostra anterior)
  // - Se diff < -180: provavelmente saiu de perto de 360 e foi para perto de 0
  if (diff > 180) voltas--;
  else if (diff < -180) voltas++;

  last_ang = ang_motor;

  // Angulo total do motor considerando voltas completas
  float ang_motor_total = ang_motor + voltas * 360.0;

  // Converte angulo do motor para angulo da junta considerando reducao 4:1
  float ang_junta = ang_motor_total / 4.0;

  // Aplica offset mecanico (zero fisico) da junta
  ang_junta -= 62.4;

  // Normaliza para 0..360 usando resto (fmod)
  ang_junta = fmod(ang_junta, 360.0);
  if (ang_junta < 0) ang_junta += 360.0;

  // Define convencao de sinal para angle1 (inversao)
  float angle1 = -ang_junta;

  // Normaliza novamente para 0..360
  angle1 = fmod(angle1, 360.0);
  if (angle1 < 0) {
    angle1 += 360.0;
  }

  // Sensor 2: leitura simples, com offset e normalizacao
  selectI2CChannel(1);
  uint16_t raw2 = as5600_2.readAngle();
  float angle2 = mapAngleTo360(raw2) - 278.2;

  if (angle2 < 0) {
    angle2 += 360.0;
  }

  // Sensor 3: leitura simples, offset e normalizacao via fmod
  selectI2CChannel(2);
  uint16_t raw3 = as5600_3.readAngle();
  float angle3 = mapAngleTo360(raw3) - 290.5;

  angle3 = fmod(angle3, 360.0);
  if (angle3 < 0) {
    angle3 += 360.0;
  }

  // -------------------------------------------------------------------------
  // 5) Angulos fixos para juntas nao sensorizadas (juntas 4..6)
  // -------------------------------------------------------------------------
  float angle4 = 0.0;
  float angle5 = 0.0;
  float angle6 = 0.0;

  // -------------------------------------------------------------------------
  // 6) Envia angulos ao Nextion (t0..t5)
  // -------------------------------------------------------------------------
  t0.setText(String(angle1, 1).c_str());
  t1.setText(String(angle2, 1).c_str());
  t2.setText(String(angle3, 1).c_str());
  t3.setText(String(angle4, 1).c_str());
  t4.setText(String(angle5, 1).c_str());
  t5.setText(String(angle6, 1).c_str());

  // -------------------------------------------------------------------------
  // 7) Converte graus para radianos (necessario para sin/cos)
  // -------------------------------------------------------------------------
  float thetas_rad[6] = {
    angle1 * PI / 180.0,
    angle2 * PI / 180.0,
    angle3 * PI / 180.0,
    angle4 * PI / 180.0,
    angle5 * PI / 180.0,
    angle6 * PI / 180.0
  };

  // -------------------------------------------------------------------------
  // 8) Montagem das matrizes A1..A6 (transformacoes homogeneas DH)
  // -------------------------------------------------------------------------
  // Cada Ai representa a transformacao do elo i-1 para o elo i.
  // Voce ja embutiu offsets (ex: theta2 - PI/2, theta6 + PI) e parametros a/d/alpha.

  double A1[4][4] = {
    {cos(thetas_rad[0]), -sin(thetas_rad[0])*cos(-PI/2),  sin(thetas_rad[0])*sin(-PI/2),  0*cos(thetas_rad[0])},
    {sin(thetas_rad[0]),  cos(thetas_rad[0])*cos(-PI/2), -cos(thetas_rad[0])*sin(-PI/2),  0*sin(thetas_rad[0])},
    {0,                   sin(-PI/2),                   cos(-PI/2),                     0.3991},
    {0,                   0,                            0,                              1}
  };

  double A2[4][4] = {
    {cos(thetas_rad[1]-PI/2), -sin(thetas_rad[1]-PI/2)*cos(0), sin(thetas_rad[1]-PI/2)*sin(0), 0.448*cos(thetas_rad[1]-PI/2)},
    {sin(thetas_rad[1]-PI/2),  cos(thetas_rad[1]-PI/2)*cos(0), -cos(thetas_rad[1]-PI/2)*sin(0), 0.448*sin(thetas_rad[1]-PI/2)},
    {0,                        sin(0),                       cos(0),                       0},
    {0,                        0,                            0,                            1}
  };

  double A3[4][4] = {
    {cos(thetas_rad[2]), -sin(thetas_rad[2])*cos(-PI/2),  sin(thetas_rad[2])*sin(-PI/2), 0.042*cos(thetas_rad[2])},
    {sin(thetas_rad[2]),  cos(thetas_rad[2])*cos(-PI/2), -cos(thetas_rad[2])*sin(-PI/2), 0.042*sin(thetas_rad[2])},
    {0,                   sin(-PI/2),                   cos(-PI/2),                     0},
    {0,                   0,                            0,                              1}
  };

  double A4[4][4] = {
    {cos(thetas_rad[3]), -sin(thetas_rad[3])*cos(PI/2),  sin(thetas_rad[3])*sin(PI/2),  0*cos(thetas_rad[3])},
    {sin(thetas_rad[3]),  cos(thetas_rad[3])*cos(PI/2), -cos(thetas_rad[3])*sin(PI/2),  0*sin(thetas_rad[3])},
    {0,                   sin(PI/2),                    cos(PI/2),                    0.451},
    {0,                   0,                             0,                             1}
  };

  double A5[4][4] = {
    {cos(thetas_rad[4]), -sin(thetas_rad[4])*cos(-PI/2),  sin(thetas_rad[4])*sin(-PI/2),  0*cos(thetas_rad[4])},
    {sin(thetas_rad[4]),  cos(thetas_rad[4])*cos(-PI/2), -cos(thetas_rad[4])*sin(-PI/2),  0*sin(thetas_rad[4])},
    {0,                   sin(-PI/2),                    cos(-PI/2),                     0},
    {0,                   0,                             0,                              1}
  };

  double A6[4][4] = {
    {cos(thetas_rad[5]+PI), -sin(thetas_rad[5]+PI)*cos(0),  sin(thetas_rad[5]+PI)*sin(0), 0*cos(thetas_rad[5]+PI)},
    {sin(thetas_rad[5]+PI),  cos(thetas_rad[5]+PI)*cos(0), -cos(thetas_rad[5]+PI)*sin(0), 0*sin(thetas_rad[5]+PI)},
    {0,                      sin(0),                        cos(0),                       0.082},
    {0,                      0,                             0,                             1}
  };

  // -------------------------------------------------------------------------
  // 9) Cinematica direta: T = A1*A2*A3*A4*A5*A6
  // -------------------------------------------------------------------------
  double T[4][4];
  multiplyMatrices(A1, A2, T);
  multiplyMatrices(T, A3, T);
  multiplyMatrices(T, A4, T);
  multiplyMatrices(T, A5, T);
  multiplyMatrices(T, A6, T);

  // -------------------------------------------------------------------------
  // 10) Extrai posicao do efetuador (x,y,z) da ultima coluna da matriz T
  // -------------------------------------------------------------------------
  float x = T[0][3];
  float y = T[1][3];
  float z = T[2][3];

  // -------------------------------------------------------------------------
  // 11) Envia x,y,z ao Nextion (t6..t8)
  // -------------------------------------------------------------------------
  t6.setText(String(x, 3).c_str());
  t7.setText(String(y, 3).c_str());
  t8.setText(String(z, 3).c_str());
}
